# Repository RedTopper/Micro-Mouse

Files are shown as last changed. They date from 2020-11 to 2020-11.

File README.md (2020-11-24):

# Micromouse (sddec20-28)
This repository contains most of the work done by Senior Design group dec20-28
during the Spring/Fall 2020. 

## Team Members
* Joshua Wooi
* Austin Chesmore
* Aaron Walter
* Richard Anderson
* Tyler Fuchs
* Jorge Gomez

## Website
[sddec20-28.sd.ece.iastate.edu](Senior Design Website)

## Resources
This repository contains additional resources generated during the project.
They are stored inside the `resource` directory in the repository root. The
contents of the folders are as follows:

### resource/alg
A\* and Floodfill Algorithms

This is a standalone implementation of the pathfinding algorithm. You can compile
it with `make`. See the README.md inside this directory for more information

### resource/docs
Documentation Files

This folder contains general information about the project, such as a setup guide,
final report, poster, and anything else documentation wise.

### resource/gui
Past User Interface Files

This directory contains a prototype GUI written in Python. We no longer use it in
favor of a web-based UI, but we will keep it here for archival purposes.

### resource/pcb
Current, Past, and Future PCB Designs

These are the Eagle files used to manufacture the PCB of the robot.

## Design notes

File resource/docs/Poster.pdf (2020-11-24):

Richard Anderson, Austin Chesmore, Tyler Fuchs , Jorge Gomez, Aaron Walter, Joshua Woo

# MicroMouse

### Problem Statement:

The goal is to demonstrate how the
interconnection of hardware and software can function together to accomplish a task. In doing so raising interest in related majors.

Client: Dr. Phillip Jones
Advisor(s): Dr. Phillip Jones | sddec20-28

### Technical details:

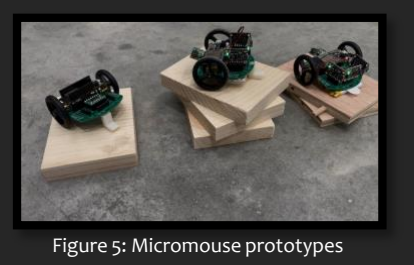
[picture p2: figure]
Figure 5: Micromouse prototypes

GUI: HTML/JS via JSON/WebSockets Framework: C++ (Async)
Floodfill: C++
A*: C++
PCB: Eagle

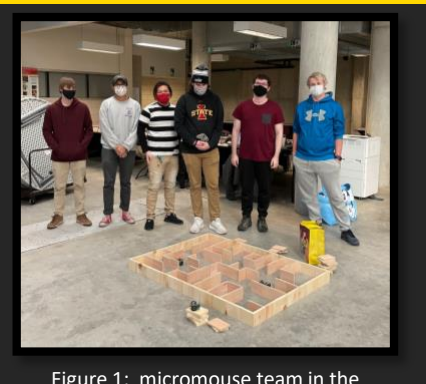
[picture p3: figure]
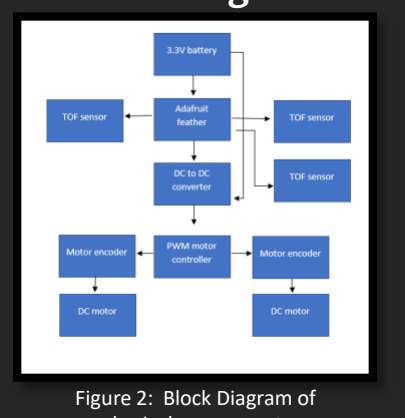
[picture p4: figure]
Figure 2:; Block Diagram of

### Functional Requirements

- Be able to navigate a maze as fast as possible both autonomously and manually.
- Show the location of the mouse in the maze
- Be able to scan for nearby walls forwards and on its sides.
- Move forward, backwards, and turn

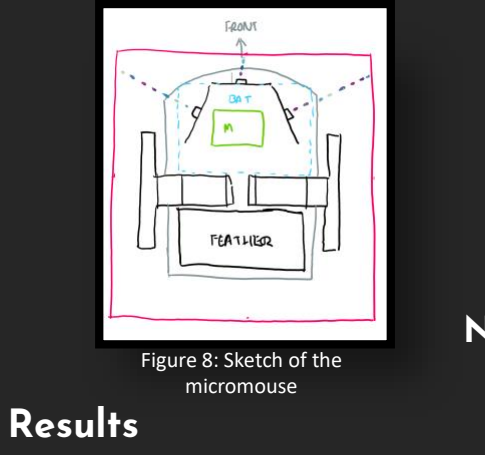
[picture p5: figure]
Results; Figure 8: Sketch of the micromouse

### Non-Functional Requirements

- The path taken towards the maze goal should be optimized in order to be solved as fast as possible
- The mouse will use A* floodfill algorithms to solve the maze.

### Intended user

The intended user of the
micromouse are potential students visiting Iowa State.

### Block Diagram

### Design approach

Our design approach was to select components and hardware that would allow us to build software that would work native. To solve this we selected an Adafruit feather that would work on C++ firmware. And a User interface that would connect to the web server built on the micro controller.

### Testing

Hardware
- Tested the individual hardware components , before testing the components together

Software
- googletest Unit Testing
- Console output for C++ and log files for JavaScript

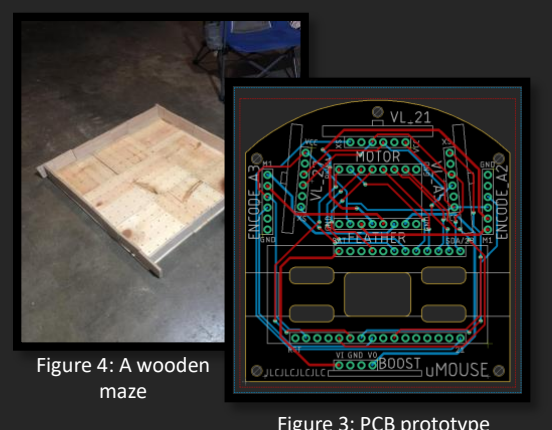
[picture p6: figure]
Figure 4: A wooden maze

Figure 3: PCB prototype

Richard Anderson, Jorge Gomez, Joshua Wooi, Tyler Fuchs, Aaron Walter, Austin Chesmore

For the micromouse project the team dealt with the challenges of working remote during the covid-19 pandemic to deliver a full hardware functional micromouse. The prototype is fully gamepad controllable and can utilize Time of Flight sensors to see obstacles.

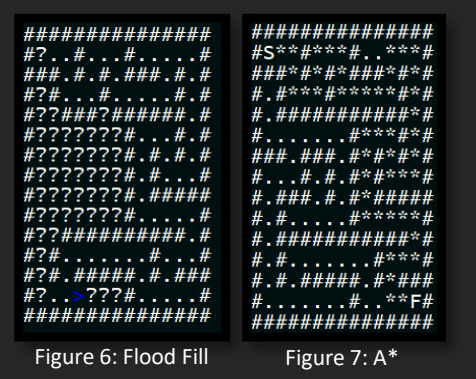
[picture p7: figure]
Figure 6: Flood Fill; Figure 7: A*

Additionally, the team has created functional software for A* and flood fill algorithms that can be implemented on the micromouse in the future

physical components

Figure 1: micromouse team in the order of the names written above

### Flood Fill & A* Traversals

The mouse runs through the Maze using modified flood fill (left), and then uses A* to find the shortest path using the filled map.

### Conceptual Sketch

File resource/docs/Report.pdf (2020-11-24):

# MicroMouse Maze Runner

FINAL REPORT

### Team number: sddec20-28 Client: Dr. Phillip Jones Advisor(s): Dr. Phillip Jones

### Team Members Joshua Wooi Austin Chesmore Aaron Walter Richard Anderson Tyler Fuchs Jorge Gomez

### Team Email sddec20-28@iastate.edu

### Team Website sddec20-28.sd.ece.iastate.edu

### Revised: 2020-11-15

# Table of Contents

1. Introduction | 4
1.1 Acknowledgement | 4
1.2 Problem & Project Statement | 4
1.3 Operational Environment | 4
1.4 Requirements | 5
1.4.1 Engineering Constraints | 5
1.4.2 Functional Requirements | 5
1.4.3 Non-Functional Requirements | 5
1.5 Intended Users & Uses | 5
1.6 Expected End Product & Deliverables | 5
1.7 Relation to Products | 6
2. Specifications & Analysis | 7
2.1 Proposed Approach | 7
2.2 Design Analysis | 7
2.3 Conceptual Sketch | 8
3. Implementation Details | 8
3.1 Previous Work & Literature | 8
3.2 Technology Considerations | 8
3.3 Possible Risks & Risk Management | 9
3.4 Expected Results & Validation | 9
4. Timeline, Resources, & Challenges | 10
4.1 Project Timeline | 10
4.2 Feasibility Assessment | 11
4.3 Team Member Contributions | 12
4.4 Other Resource Requirements | 12
4.5 Financial Requirements | 13
5 Testing and implementation | 14
5.1 Hardware and software description/build | 14
5.2 Hardware Details | 15
5.3 Software Details | 18
5.3.1 Device Firmware | 18
5.3.2 Flood Fill | 19
5.3.3 A* | 19

### SDDEC20-28 1

5.4 Maze Design | 20
5.5 PCB Design | 21
5.5.1 Circuit Schematic | 21
5.5.2 PCB | 22
5.6 Testing Process | 22
5.7 Results | 22
6. References | 26
Appendix I | 27
Operation Manual | 27
Appendix II | 29
Alternative/Initial Version | 29
User Interface | 29
Maze | 31
Appendix III | 32
Tyler | 32
Jorge | 33
Austin | 33
Richard | 33
Aaron | 33
Joshua | 34
Appendix IV | 34

# Figures & Tables

1. Figures
Figure 2.1 High-Level Schematic Design of MicroMouse Prototype | 8
Figure 4.1 Gantt Chart showing timeline | 11
Figure 4.2 Final Bill of Materials and related costs | 13
Figure 5.1 First Prototype Build | 14
Figure 5.2 Breadboard Prototype Build | 14
Figure 5.3 Final Prototype Design | 15
Figure 5.4 Micromouse Ski | 15
Figure 5.5 Micromouse Components | 16
Figure 5.6 Physical Maze Assembled for Prototype Testing | 20
Figure 5.7 Circuit Schematic for Prototype | 21
Figure 5.8 PCB Version 2 | 22
Figure A.1 CLion | 28
Figure A.2 Micromouse Connection | 29
Figure A.3 Micromouse Prototype | 29
Figure A.4 UI version 1. Simple layout | 31
Figure A.5 UI version 2 of the prototype. Web address added | 31
Figure A.6 Version 3 of the UI | 32
Figure A.7 Maze Panels | 33
Figure A.8 Code Part 1 | 36
Figure A.9 Code Part 2 | 36
Figure A.10 Virtual Maze Design | 36
Figure A.11 Virtual Maze Layout | 37
Figure A.12 Virtual Micromouse in Blender | 37
Figure A.13 Importing prototype into Unity | 37
Figure A.14 Standard Floodfill algorithm | 38
Figure A.15 Modified Floodfill | 38
Figure A.16 Goal Searching | 39
2. Tables
Table 4.1 Deliverables Schedule | 10
Table 4.2 Personal Effort Requirement | 12

. Introduction
1.1 ACKNOWLEDGEMENT

This section acknowledges Dr. Philip Jones for his contributions in providing technical advice to the team and Lee Harker for his guidance in sourcing hardware parts and using the EAGLE software. In addition, we would like to thank Jeremy Thurlby and his workshop who helped create feedback for the physical maze design and cutting the maze tiles.

1.2 PROBLEM & PROJECT STATEMENT

Problem Statement:
Our client has outlined a robot that will be able to navigate a maze and autonomously decide and calculate the fastest path to the goal of the maze. This mouse must be able to navigate the maze and run the maze with the fastest path available. This mouse will need to demonstrate how the interconnection of hardware and software can function together to accomplish a task.

Solution Approach:
A MicroMouse Maze Runner Showcase.

People project that there will be many more computer/electrical/software-based jobs than there are people to fill the jobs, so we need to try to give a reason for future ISU students to consider robotics-based curriculums. This project serves to showcase the capabilities of engineering students from multiple disciplines at Iowa State University.

The expected outcome of this project is a functioning micromouse unit(s), capable of both autonomous and/or remote-control functions, that can traverse through several different maze designs effectively. Our expected outcome was near our completed design, but there were some major missed goals of our project. The main goal that we were not able to accomplish was the traversal of the maze autonomously. While our micromouse can navigate the maze with controller input, we were not able to finish the autonomous version of the maze navigation. We also did not finish a graphical user interface. The client outlined a GUI to draw the maze and update in real time, but we never finished this feature.

1.3 OPERATIONAL ENVIRONMENT

The product of this project was to be able to operate a micromouse in a controlled environment. We designed the maze to have a smooth surface with adjustable walls. This will ensure the maze is stable for the micromouse to navigate. The operation of a micromouse outside of this environment condition is unexpected and undesired. We expect the environment to be modular and transportation friendly so people can use it anywhere with enough space.
1.4 REQUIREMENTS

### 1.4.1 Engineering Constraints

| ● The memory size on the Feather was a strict 520 kb

- The ROM size of the Feather is 4MB
- The micromouse requires a flat smooth surface for the maze
- Hardware is inherently unreliable

### 1.4.2 Functional Requirements

Functional requirements of this project would be that the mouse is able to move through the maze, is able to map a maze to a maze model, is able to find the shortest path of the maze model and is able to follow paths through the maze. We also must have a maze that can fit the micro mouse, be modular, transportable, and solvable by the mouse.

### 1.4.3 Non-Functional Requirements

Non-Functional requirements of the project are that the mouse should be accurate, reliable, and sturdy. Our maze will have to be of quality materials so that it is able to last long when we reconfigure or transport it.

1.5 INTENDED USERS & USES

As a showcase project, the intended user of a micromouse is anyone with latent interests in Robotics. Our team designed this project to inspire and encourage anyone to pursue a degree in the STEM field.

1.6 EXPECTED END PRODUCT & DELIVERABLES

During this project there were many timelines that COVI-19 forced us to change due to circumstances we had no control over. Therefore, some deliverables were either delayed indefinitely or removed entirely from the scope.

Components ordering (2/21):
We submitted our Bill of Materials for ETG to approve, so we can continue to make progress on Prototype 1.

Delay (3/20)
When classes transitioned into a virtual environment, we had to delay the deliverables with Prototype 1 and all future hardware related operations until further notice, since the university had implemented safety precautions against COVID by closing access to the lab equipment on campus to students.

GUI (3/27)
The team created and delivered the first prototype of the GUI to the client.

Virtual Maze (3/27)

The team developed a virtual maze and robot with the unity engine so work could continue the prototype’s embedded algorithm while conforming with virtual instruction guidelines.

GUI 2 Electric Boogaloo (4/10)
The team designed the GUI to be more user-friendly and included a mapped maze.

Hardware Constructed (4/18)
The team constructed the parts to ensure everything was functioning as expected.

Second Round of Parts (9/15)
The team ordered a second round of parts as a contingency for technical failures during tests.

Software Testing (9/29)
The team began software testing on the Feather so that we can continue to develop hardware and software integration.

Maze cut & Assembled (10/10)
The team cut the physical maze and assembled it to test the micromouse once we completed the prototypes.

PCB Design (10/27)
The team ordered, received, and assembled our first prototype on a working PCB.

Prototype Assembly (11/6)
The team delivered a working prototype that someone can control with an Xbox One controller to the client.

1.7 RELATION TO PRODUCTS

We expect that a competition-ready micromouse will have various iterations before it is up to professional standards. The team believes that there is still room for improvements on our first prototype, and it is therefore unfit for a micromouse contest. That said, we believe that this prototype has met all the requirements and expectations of our client’s project. A micromouse should not be more than 25cm by 25cm, in length and width, with no restrictions on the height of the micromouse. Also, it must use a source of energy that does not involve a combustion process. Next, the micromouse should not leave behind parts of itself in the maze while solving it. Lastly, micromice should not jump, fly, or climb over any walls, and it should not burn, cut, or damage the walls of the maze or maze itself. This mouse is 10.2cm x 10.2cm which is smaller than most other micromouse units. Furthermore, a lithium-ion 3.7V battery powers the mouse.

## 2. SPECIFICATIONS & ANALYSIS

2.1 PROPOSED APPROACH

The team decided to prototype the project using an Adafruit Feather as a controller, to allow for a more robust implementation using the Feather’s features. The team also chose the Feather since it can support all the peripherals for the project, such as I2C signal bus, and analog to digital signal conversions. The feather also has built in support for Bluetooth and Wi-Fi functionalities that satisfies the requirements of our client for an optional wireless communication system with a user.

We had two prototyping phases for hardware in this project. The first phase was assembling components on a breadboard, and the second phase was designing and having a PCB fabricated. The plan when starting the project was to use Python to interface the software and hardware, due to the flexibility of the language in its compatibility with other types of software. For instance, we would write the maze algorithm, the GUI, and hardware interface in Python with different libraries. Additionally, we utilize C++ along with several Arduino libraries to program the functionalities of the micromouse.

We ordered an additional set of components, so that we would have spares if potential errors or hardware malfunctions occur.

2.2 DESIGN ANALYSIS

During the first semester, the project team thoroughly researched the specifications that the Micromouse project will need to meet. Through this research, the team developed a components list. We brought the component list for approval by Dr. Jones and ETG, to ensure that the selected components were reasonable for the purposes of the project. In the second semester, the team focused on testing the components and integrating them into a full micromouse prototype. At the end of the second phase of the design process the team transitioned into testing integration of software and hardware to ensure functionality. At this point, the team decided to split into two branches for software and hardware. Towards the end of the project, the team converged both branches back together to reintegrate the software and hardware side of the project.

2.3 CONCEPTUAL SKETCH

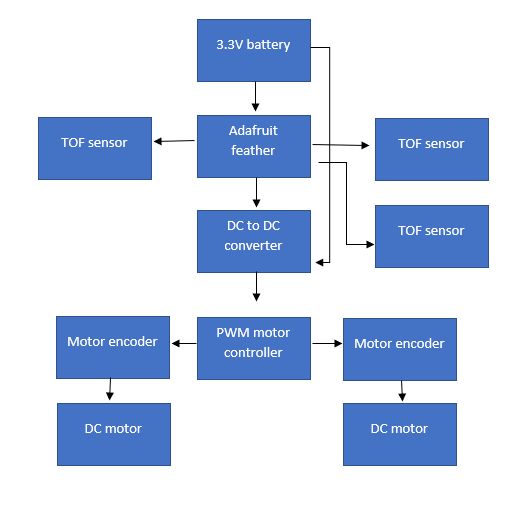
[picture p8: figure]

Figure 2.1 High-Level Schematic Design of MicroMouse Prototype

This is a conceptual design of how the micromouse will be created and interact with all the components that were selected by the tram for the project. It shows how the micromouse functionality will live on the Adafruit feather, while the feather will then command the other components to enable the micromice hardware functionality

## 3. IMPLEMENTATION DETAILS

3.1 PREVIOUS WORK & LITERATURE

Classwork here at Iowa State University has laid a foundation that we can reference, specifically CprE 288 in its autonomous robot project. This project has had a long history, and there are plenty of online articles and documentation that will help us in designing the micromouse. There are also micromouse competitions that should yield even more documentation that our team can reference for our project. For our PCB design we utilized a software program called Eagle and referenced a tutorial by Jim Blom (Blom, Jim).

3.2 TECHNOLOGY CONSIDERATIONS

The technology that we incorporated for our micromouse was cost effective and modular. The team selected widely available components to integrate it into the prototype design. By using off the shelf components, the project will less likely have quality issues, such as solder bridging or improper design. This removes several potential failure points, allowing for the project to be bug tested more effectively. However, one weakness of using these types of components is that there is less controllability of the specification.

Other considerations include the amount of memory available to our team on the feather. We need to be diligent on how large our software is and how much memory it will consume when running the maze.

3.3 POSSIBLE RISKS & RISK MANAGEMENT

Prototyping the mouse was the most worrisome of our project, getting all the different pieces to work together included. After we learned what hardware can work with what software, prototyping became much easier and we were able to create more designs.

When we tested components, it was important to be careful as to not connect pins where they should not be. This became apparent when a team member put a 12V supply on a GPIO pin and subsequently fried our first Feather. Other risks include damage to our components, when moving them they needed to be either secured in a safe storage container, or back in the foam protection they came packaged with. Luckily, we did not have any issues with bent pins from transportation.

Cost was a major part of our potential risk when designing our micromouse robot. The cost to the maze can range from 10s to 100s of dollars. We only ended up spending about $40 on the maze itself but looking back we should have spent more.

The final risk that we considered was that none of our members of our team had any prior experience with PCB design. This was why our team spent many weeks designing the PCB. To mitigate this risk, we had two team members, with instructions from our mentor, build and practice with Eagle software to become more efficient.

3.4 EXPECTED RESULTS & VALIDATION

The desired outcome, as outlined by the client, is a micromouse that can solve and run through a maze on its own. It will also have a display that people will use to run the program and can respond to user input. The user will have the ability to control the mouse with a controller and the mouse will respond accordingly.

## 4. TIMELINE, RESOURCES, & CHALLENGES

4.1 PROJECT TIMELINE

Table 4.1 Deliverables Schedule

Dates | Deliverables
1/20-2/21 | We constructed our groups and scheduled bi-weekly meetings with the clients. The team researched parts for the robot prototype and ordered them. The team began prototyping.
2/22-3/20 | The university transitioned to online formats and this included our team. We developed a virtual platform for our micromouse to navigate a maze and allowed us to test any maze path finding.
3/21-4/10 | Prototypes of the GUI, maze and Virtual maze delivered to the client. The team decided to move work to a virtual platform built in Unity due to COVID-19.
4/11-4/18 | Our team received our parts after COVID-19 delayed them. Hardware testing began with breadboard and components.
4/19-5/2 | Project Design Document drafted and finished; Project website updated.
Break | Summer Break
8/20-8/31 | The team scheduled meetings with the client.
9/1-9/14 | Our team Encoders tested. Round 2 of parts ordered.
9/15-9/28 | GUI connecting via Wi-Fi, microcontroller code continuing. PCB design beginning. Hardware testing continued. Round 2 of parts received.
9/29-10/9 | A* algorithm developed. Updated version of GUI developed. Web server on feather developed and tested.
10/10-10/26 | Maze cut and assembled. Final GUI developed to incorporate a maze drawing panel. First version of PCB design and presented. A* finalized. Modified flood fill development.
10-27 - 11/9 | PCB delivered. Prototype 1,2, and 3 fabricated. Input to micromouse demonstrated to the client. Modified flood fill finalized.
11/10-11/19 | Prototype 1 & 2 fully functional. Project Document drafted and finished. Build Guide created for future teams.

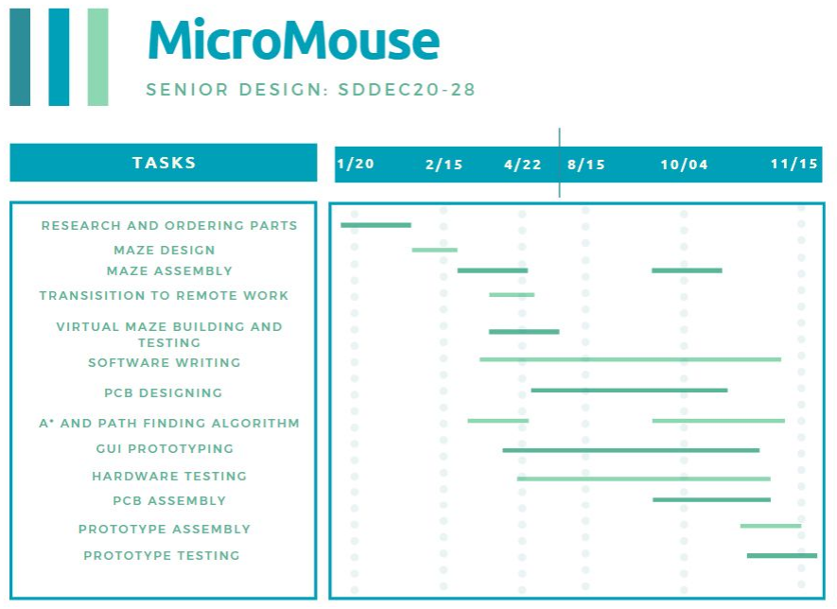
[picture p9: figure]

Figure 4.1 Gantt Chart showing timeline

4.2 FEASIBILITY ASSESSMENT

- Autonomous maze navigation
- Wall detection without getting stuck in a loop
- Detecting the goal of the maze
- User input controls
- Bluetooth protection from other devices
- Maze Design
- Price - keeping the price in check so we do not blow the budget.
- Mobility - being able to transport the maze while also being large enough to be complex

4.3 TEAM MEMBER CONTRIBUTIONS

Table 4.2 Personal Effort Requirements

4.4 OTHER RESOURCE REQUIREMENTS

The main outside concern is where we can store the maze while it is being built. As per the client, they would like a maze that is at least 9 feet by 9 feet, so this will require a large open space.

Team Member | Contribution | Prev semester | This semester | Total
Richard Anderson | My contributions were the algorithms for the micromouse, specifically the modified flood fill and A* algorithms, as well as testing the algorithms correctness and modifiability to for hardware use | 47 | 75 | 122
Austin Chesmore | My contributions to the project we to primarily assist with testing the hardware components. I also assisted with assembling/soldering of the prototypes and the component selection | 53 | 105 | 158
Tyler Fuchs | My main contribution to the group was working on the UI in its many forms and building the physical maze. In total I built 4 different UIs to test and two sets of maze walls. | 42 | 91 | 133
Jorge Gomez | My greatest contribution to the team was the scouting of hardware and PCB research and design. | 41 | 74 | 115
Aaron Walter | My contribution was writing the firmware for the feather. I got a mini web server working on the Feather and all of the “drivers” written to work with the hardware. I also helped a lot with the PCB designs. | 57 | 117 | 174
Joshua Wooi | My contributions were designing and revising the PCBs and some of the soldering work. | 37 | 70 | 107

4.5 FINANCIAL REQUIREMENTS

For the Micromouse project our budget is set at $500 per semester with the ability to extend beyond if we need to. The team split the budget between the hardware and physical components. We decided to construct the maze from rough cut pine to keep the price down. In total the physical maze ran a price tag of $32.15. Whereas someone can use the hardware between different prototypes. During the first half of the project the team spent $316.87 on the hardware components. On the other hand, we used $320.42 for the second set of components. In the end the sum cost of all hardware came to a cost of $605.14. As depicted in Figure 4.2, one of the greatest costs is the ToF sensors. We found a different component for future use. The suggestion is to go from using the VL6180 ToF sensors by Adafruit and moving towards using the VL680X ToF sensor from Pololu causing the price of sensors to go from $13.95 per sensor to $8.49 per sensor. Overall, the team kept costs the allowed amount and new, cheaper components are being thought of for future use.

Figure 4.2 Final Build of Materials and Related Cost

Item# | Item type | Qty | Cost | Subtotal | Part# | Supplier | Supplier#
1 | Feather board | 4 | $20.95 | $83.80 | 3591 | Digi-Key | 1528-2514-ND
2 | Motor Controller | 4 | $3.42 | $13.68 | 713 | Digi-Key | 2183-713-ND
3 | Magnetic Encoder | 8 | $7.95 | $63.60 | 4761 | Digi-Key | 2183-4761-ND
4 | Wheels | 8 | $3.75 | $30.00 | 1452 | Digi-Key | 2183-1452-ND
5 | Motors | 8 | $18.95 | $151.60 | 3053 | Digi-Key | 2183-3053-ND
6 | DC/DC 3.7 to 12v | 4 | $2.99 | $11.96 | | Canton Electronics
7 | ToF Sensors | 12 | $13.95 | $167.40 | 3316 | Digi-Key | 1528-1815-ND
8 | Battery 3.7v (4.2) | 4 | $9.95 | $39.80 | PRT-1381 3 | Digi-Key | 1568-1492-ND
9 | Encoder Wires | 8 | $0.95 | $7.60 | 4762 | Digi-Key | 2183-4762-ND
10 | .3.6-pin 0.1" Short Break-away Male Header - Pack of 10 | 2 | 4.95 | $9.90 | 3009 | adafruit
11 | 36-pin 0.1" Short Female Header -Pack of 5 | 2 | 7.95 | $15.90 | 3008 | adafruit
12 | 0.1" 36-pin Strip Right-Angle Female/Socket Header (5 pack) | 2 | 4.95 | $9.90 | 1542 | adafruit
| TOTAL | 62 | | $605.14

## 5 TESTING AND IMPLEMENTATION

5.1 HARDWARE AND SOFTWARE DESCRIPTION/BUILD

Testing of the hardware components and assembling several testing prototypes was necessary to ensure that the teams ordered components would function correctly. At an early point in the project the team moved towards creating a virtual maze environment that team members could test the micromouse in. During this time, another team member was constructing the physical maze. However, the team ended up testing the first hardware prototype with limited functionality due to component shipping wait times, and thus the team scrapped the virtual maze for testing and transitioned into the physical maze.

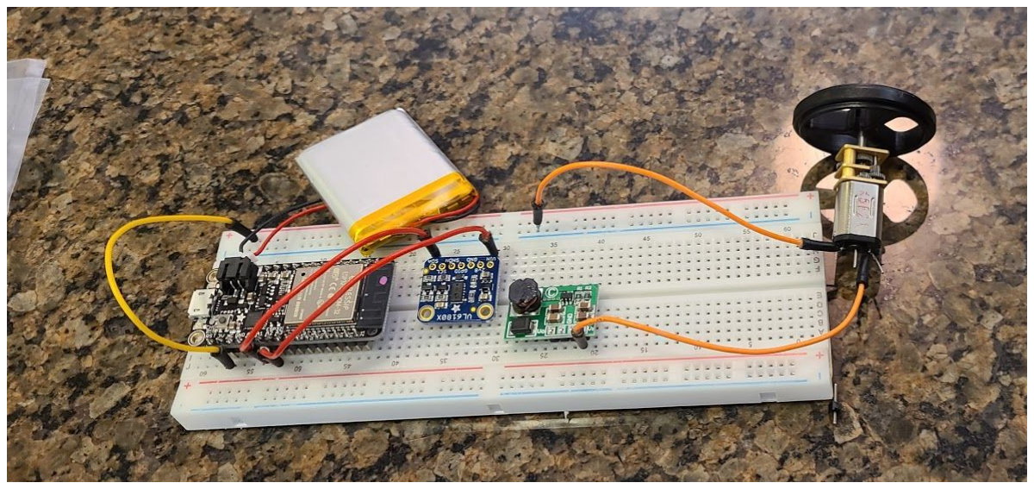
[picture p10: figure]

Figure 5.1 First Prototype Build

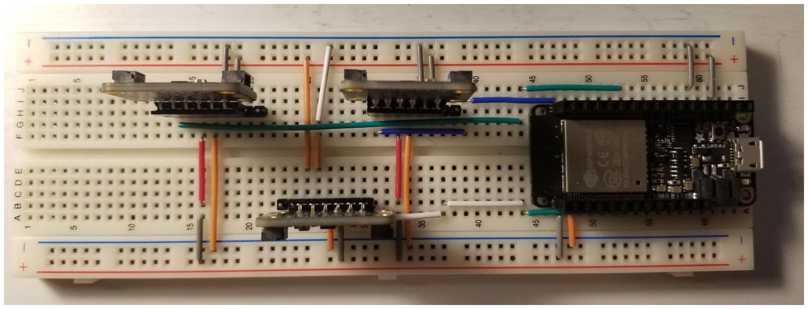
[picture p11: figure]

Figure 5.2 Breadboard Prototype Build

This hardware prototype at the end of semester one used a breadboard and the available components, for basic proof of concept design tests. We only incorporated a single wheel and sensor into the design to demonstrate that all components work together as intended. Additionally, after the first round of testing, the team would then move to a more permanent hardware design using PCB instead of the breadboard.

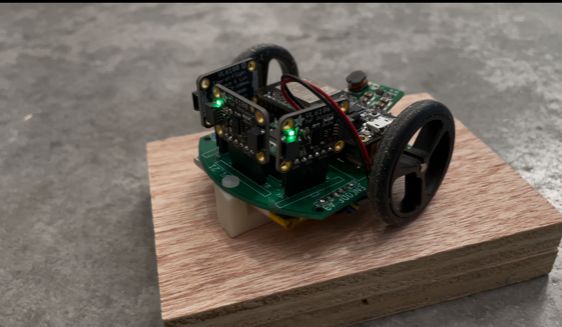
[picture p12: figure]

Figure 5.3 Final Prototype Design

The current micro mouse design is currently being prototyped using a final PCB design for proof-of-concept design tests. The team integrated all components onto the PCB along with a 3D printed ski. For this prototype we were able to utilize the C++ software that was written by the team to achieve movement functionality.

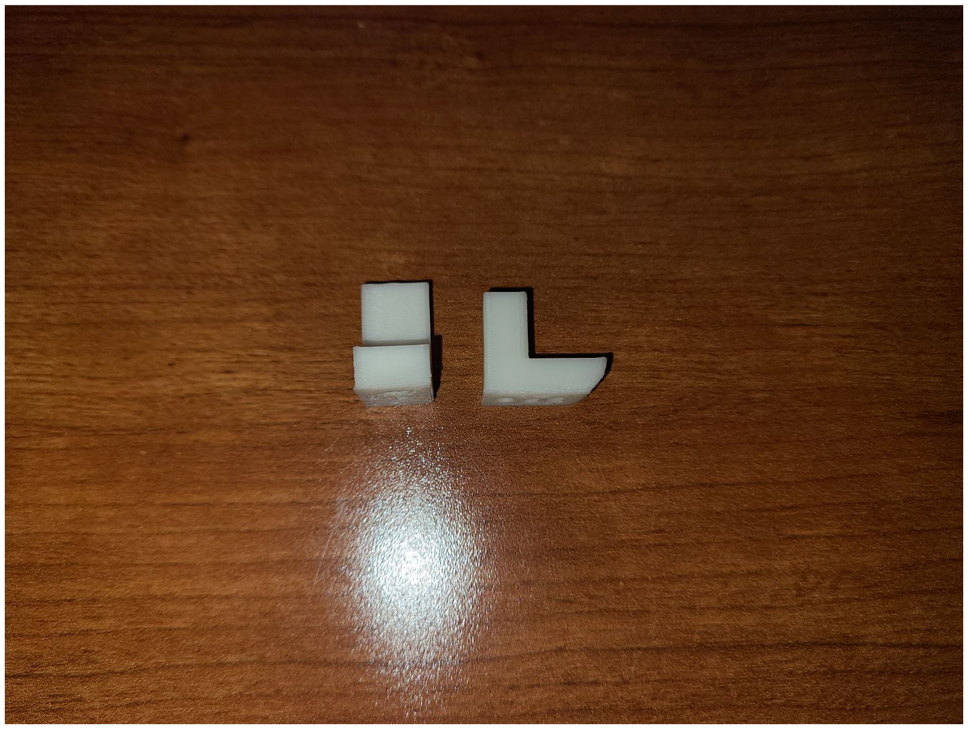
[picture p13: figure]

Figure 5.4 Micromouse Ski

Additionally, the project team 3D printed a ski that is seen implemented in figure 5.2. This ski allowed the prototype design to function with only 2 wheels, while also allowing for improved stability.

5.2 HARDWARE DETAILS

The team selected the components members could easily integrate them into the micromouse. By using prebuilt components, we reduced the risk of having issues with the quality of the components. This would allow for the team to focus on the main objectives, rather than having to troubleshoot smaller issues such as faulty components.

Below, you will find a breakdown of the components used in the construction of the micromouse along with the quantity of parts used per micromouse, and the reasoning behind why the team chose them.

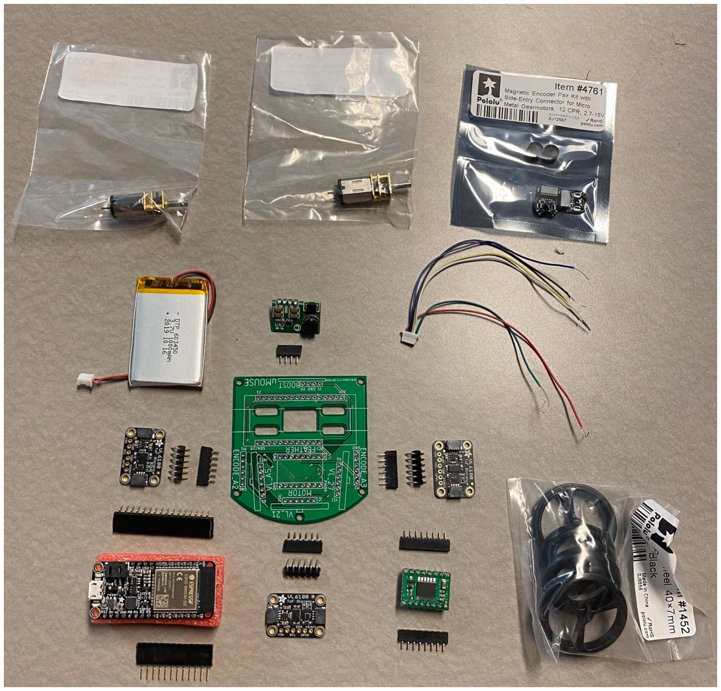
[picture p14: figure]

Figure 5.5 Micromouse Components

- HUZZAH32 ESP32 FEATHER MALE HDR
| x1
- The Adafruit Feather is a compact but powerful development board with in-built functionalities that meet all our requirements. It has Wi-Fi capabilities, programmable in C/C++, uses I

2C for the sensors, PWM for the motors, ADC/DAC pins for controls, and GPIO pins for everything else.

- TB6612FNG Dual Motor Driver | x1
- This Motor Driver can control up to two motors simultaneously and allows us to tune the rpm of the motors as needed, using feedback from the encoders.
- Magnetic Encoder Pair Kit With Side-Entry Connector for Micro Metal Gearmotors, 12
CPR, 2.7-18V | x1
- The encoders allow for precise rpm configuration and are compatible with the motor in the components list.
- WHEEL 40X7MM PAIR - BLACK | x2

- These wheels are compatible with the motors on this list. In addition, they are rubber lined and will do well on different surfaces. Lastly, the axles are made of plastic to eliminate any possible problems with the encoders.
- GEARMOTOR 220 RPM 12V METAL EXTD | x2
- These motors meet our size requirements, are powerful and fast for their size, include gearboxes, are compatible with a wide range of wheels and the encoders.
- 12W DC-DC Converter Boost 2V-12V | x1
- This boost converter increases and regulates the voltage output of the battery to supply power to the motors.
- VL6180 TIME OF FLIGHT DISTANCE
| x3
- These distance sensors use I²C for fast communication with the Feather and fit well within the size for the micromouse.
- B6-PIN FEMALE JST SH-STYLE CABLEATTERY LITHIUM 3.7V 1AH | x1
- This battery meets our needs to power the Feather, at 1000 mAh, is rechargeable, and is relatively compact.
- 6-PIN Female JST SH-STYLE Cable
- These six pin male connectors fit well with the encoders.
- 36-pin 0.1" Short Break-away Male Header (10pack) ... | x1
- These male header pins are to be soldered onto components so it can be attached to header sockets on the PCB.
- 36-pin 0.1" Short Female Header (5 pack) | x1
- These female header pins are to be soldered onto the PCB so it can accept components.
- 0.1" 36-pin Strip Right-Angle Female/Socket Header (5 pack) | x1
- These right angle male pins are to be used to allow the VL6180 Time of Flight Distance sensors to stand perpendicular to the PCB.
- PCB | x1
- The PCB was the only piece of hardware that was designed by the team for the explicit purpose of housing/organizing the above components. In doing so, it gives the micromouse a more cohesive look. We decided on using header pins/sockets style connections for a secure but impermanent connection between the PCB and the components. This was done so components can be easily replaced. This PCB was designed using Eagle, a scriptable electronic design automation application, and went
| through a few iterations before arriving at the final version that was used. More
| information on the PCB can be found in Appendix II.

5.3 SOFTWARE DETAILS

The Micro-Mouse project has multiple software components. There are three main parts, the GUI, the software to bridge the hardware devices, and the maze algorithms. Each component was essential in delivering a maze running micro-mouse that met all of our client’s requirements.

The device firmware that interfaces with the hardware components was written in C++. Many different functions were needed that were not originally foreseen when beginning the prototyping phase. For instance, a function was required to slow down the acceleration of the motor controller due to a bug that would shut down the feather if the speed was set from a stop to full speed.

The User Interface has gone through many different changes and versions. To begin the project, we had selected a GUI library in python called PyQT5 to write the graphics. The plan was to write a simple panel with a spot for a console, image holder for mapping the maze, and a few buttons for functionality. After a few versions and upgrades to this plan we ran into an issue with drawing the maze and updating it during the navigation of the maze. Instead, our group moved to developing a web-based GUI that will utilize JavaScript to run commands and access the basic web server running on the Adafruit Feather. HTML5 would provide the imaging mapper tag that would help to draw the maze and fill in the missing functionality that the PyQt library was missing.

The maze solve algorithm is used so that the mouse can navigate and then solve the maze. The algorithm first does a modified flood fill to build a maze model, and then uses an A* algorithm to find the shortest path. The algorithm is gone into further detail in section 5.3.2 and 5.3.3.

5.3.1 DEVICE FIRMWARE

The device firmware has many different components that make the device function. It implements a lightweight MVC framework written in C++.

Access Point
The first component is the AP Station software that allows the ESP32 to host a wireless hotspot for the “command center” client to connect to. The micromouse firmware can also be used to connect to a client, to then connect to an existing hotspot if needed.

Async Web Server (Controllers and Views)

The firmware also includes an asynchronous web server to allow the command center to communicate with the micromouse in real time. There are two parts to this web server: the JSON REST API and a WebSocket. The REST API allows the client to query the status of the robot: distance traveled, sensor distances, speed, and other real time information. The WebSocket allows the command center to send movement commands to the robot. The valid inputs are currently keyboard and any X-input controller.

Components (Models)
The firmware includes a lightweight “driver” for each of the devices connected to the mouse. There are components set up for the encoders, motors, and time of flight sensors. These components control the logic of the hardware and provide information to the pathfinding algorithm.

## 5.3.2 FLOOD FILL

The mouse uses a modified flood fill algorithm to scan the physical maze. How a typical flood fill algorithm works is it scans all possible directions from the current cell, and then recurses down each of the cells that are able to be visited, until every cell has been visited. This is the behavior of the typical flood fill, whose pseudocode can be found in Appendix IV.

In terms of the micromouse however, this algorithm is not satisfactory, since the mouse needs to physically move throughout the maze. With the described algorithm, the mouse would be expected to teleport back to previous cells, as well as already knowing the maze. We needed to modify this algorithm so that the wall-checking instead uses scanner distances to check for immediate walls, as well as consider mouse movement and directions, and moving the mouse to previous cells during recursion. In our implementation, we create a 2d array of binary numbers, and use the 5 rightmost bits to keep track of the north, east, south, and west walls, as well as if the related cell has been visited.

The updated flood fill starts with the mouse using its sensors to scan the immediate left, right, and forward cells from its current direction, and then adding those scan results to the maze map. From those scans, if any of them are 0 (meaning no wall), then the mouse will turn towards the “wall-less” direction (if need be), move forward 1 cell, and then recurse down in the algorithm with that cell. Once the cell has gone down each direction, the mouse turns towards the direction opposite of what the mouse was at the start of the current recursion level, then moves forward, effectively moving the mouse backwards to where it was before recursion. The cell is also marked as being visited so the mouse will not go back down the direction. The modified version of the flood fill can be found in Appendix IV

5.3.3 A*

Once the mouse has been flood filled, it can use an A* algorithm to find the shortest path from the starting position to the goal.

To find the goal of the maze, we obtain the map through the flood fill process. Then, we have another function which searches the maze map for a 2x2 closed loop, meaning we make sure that a northwest cell can go to the south and east cells, and the southeast cell can go to the north and west cells. This functionality can be seen in Appendix IV.

Once we know the end goal, we have the heuristic to be used for our A*. From there, it's a matter of getting a selected path, taken during the A* process. With this path, we will be able to get instructions that the micromouse can follow to solve the maze.

5.4 MAZE DESIGN

The client outlined that the micromouse maze needed to be mobile and reconfigurable. To combat these challenges our team designed a maze that used wood tiles/panels in combination with a peg board pattern where the walls could be moved around to create new maze patterns. This is shown in appendix II. Figure 5.6 is an image of the maze we built when testing our prototype micromouse. We did not use the maze panels for this test because we wanted a complex design for the robot to navigate through.

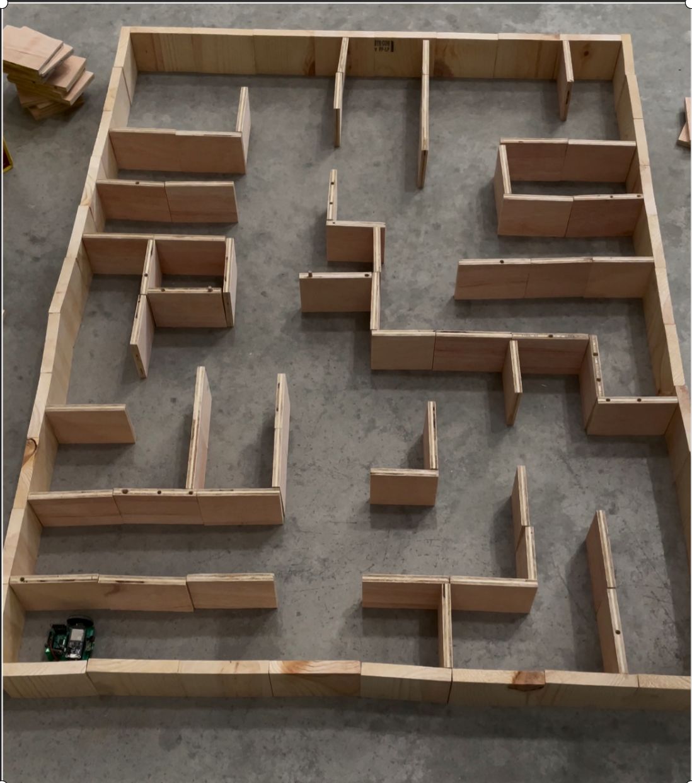
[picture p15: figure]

Figure 5.6 Physical Maze Assembled for Prototype Testing

These maze walls are the standard 3 inches high. This was found to be the standard for half size micro-mice. For the maze panels, they were cut from a 12” x 8’ board of rough-cut pine. Since it was a rough cut board we were forced to cut a little further down and the panels came out to be 11.25” x 11.25”. This required the panels to precisely cut and therefore we spoke to Jeremy Thurslby, and with his help we cut the panels using a CNC router which yields perfectly symmetrical panels that can be connected together.

## 5.5 PCB DESIGN

## 5.5.1 Circuit Schematic

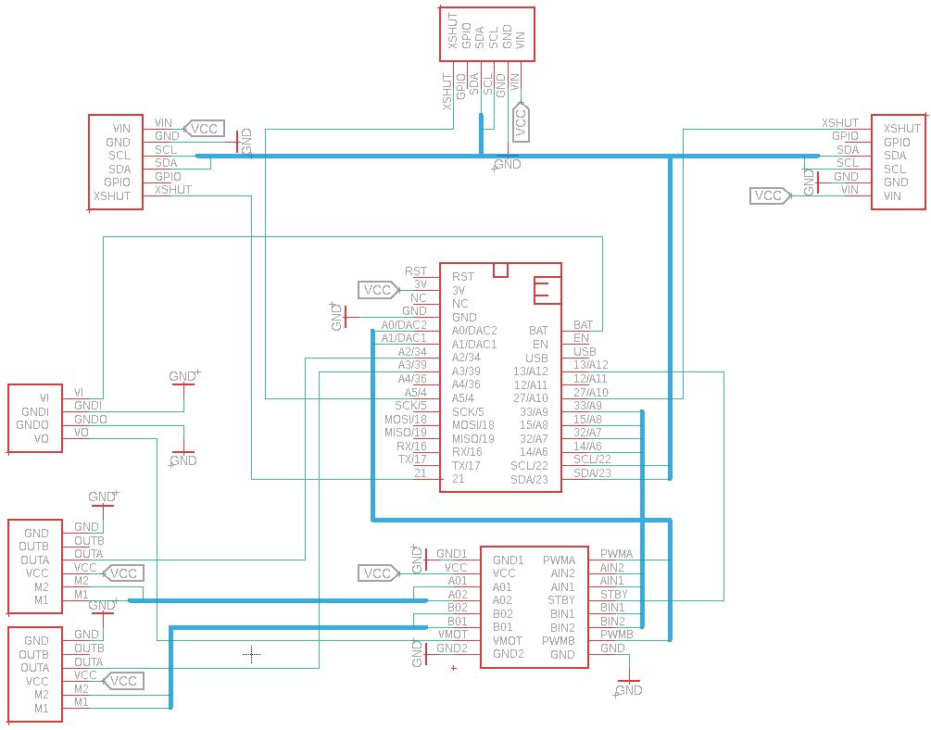
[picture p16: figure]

Figure 5.7 Circuit Schematic for prototype.

The circuit schematic file (depicted above) illustrated through Eagle, which describes a low-level interpretation of our initial design, and details the interconnections between our components in the PCB. The feather board serves as our main controller for most of the operations through the BAT, 3V, and most of the GPIO pins. The 3 distance sensors sit at the front/top and communicate with our Feather board via I2C in the SCL and SDA pins. Additionally, we allocated 3 GPIO pins as ‘XSHUT’, which will effectively shut down a targeted sensor, should we decide it is necessary. The 3V, which outputs a steady 3.3V through an in-built regulator, serves as the pull-up supply for most of the components. However, this pin is limited to a 500mAH output, which will not be sufficient to power the motors. The BAT pin, which outputs a 3.7V supply, is therefore boosted to a steady 12V to power the motors, through the motor controller. Most of the other GPIO pins are dedicated to the ADC and PWM pins which decide the rpm at which the motors operate. Feedback from the motor, provided by the encoders, is then connected to the Feather. All these components are externally powered by a 3.7V, 1000mAH rechargeable battery, which is rechargeable through the microUSB port on the Feather.

## 5.5.2 PCB

Rather than using any surface mounted pads, we created custom footprints to solely use through-hole vias to accommodate header pins. Using Eagle’s auto-routing function, we produced a layout (depicted below) that we used for our MicroMouse prototype. The produced layout had multiple vias that connected traces between the 2 copper layers, and while we had reservations about this design from an aesthetic standpoint, we do not expect that it will hinder performance in the slightest.

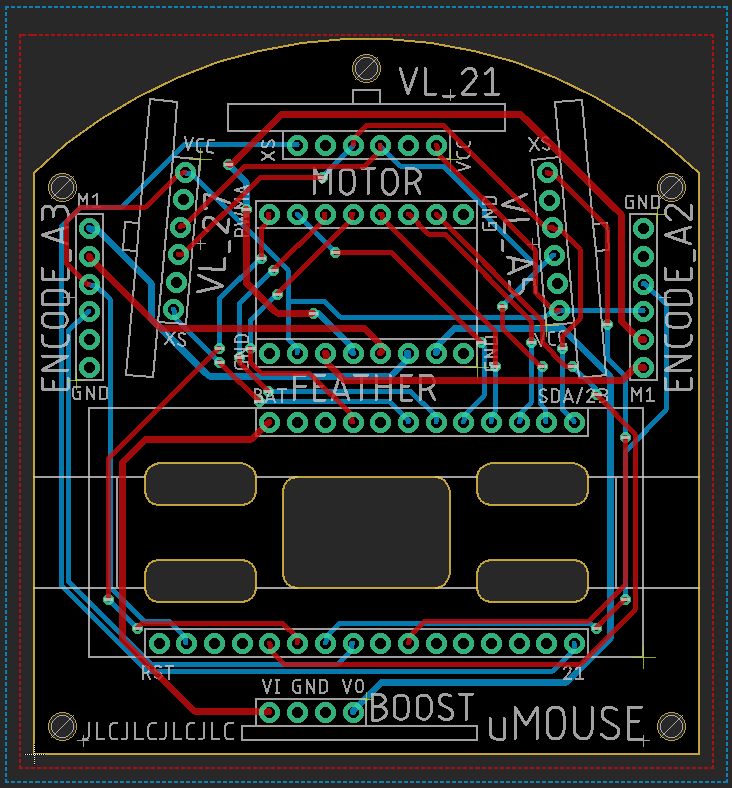
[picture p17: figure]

Figure 5.8 PCB Version 2

5.6 TESTING PROCESS

Once the software was built and flashed onto the micromouse we were able to test the basic web server that was hosted on the Adafruit Feather. An interface between the software and hardware was tested by flashing this firmware onto the mouse and seeing any changes in the robot’s responses. This development was all done in CLion as described in Appendix I. We also tested some of the hardware controllers with Google Test, which is a c++ unit testing library.

5.7 RESULTS

Throughout the duration of this project our team has put in countless hours from design planning to PCB drafting, to sawing the maze, to draft writing. Our client outlined a few main goals for us to work towards along with a project statement. The main goals we had were to:
1. Build a working micromouse that can manually navigate a maze.
2. Build a User interface so any person can test the functionality of the micromouse
3. Allow the robot to navigate the maze autonomously and choose the fastest route.

Along with these outlined criteria the team established success criteria for the team to judge the outcome of the project. While our team’s timeline and results were affected by the COVID-19 pandemic, the team persevered and met the majority of the self-imposed goals. Below is a list of the success criteria that the team created, along with the results and explanations for meeting or not meeting criteria.

### 1. Create a working micromouse design that has easily replaceable components

The results of the success criteria were that we successfully created a couple of fully operational micromouse prototypes that had easily replaceable components. this was accomplished by utilizing male and female header pins to solder to the PCB and components, as opposed to soldering all components directly to the PCB

### 2. Produce a micromouse prototype that utilizes a PCB

The result of the success criteria was positive as we received our components and started prototyping originally with breadboards. However, breadboard testing created several reliability issues with faulty connections. these “bad connections'' prevented the components from communication effectively over I2C. This pushed the team to get a PCB design created and ordered. after the PCB prototypes were integrated into the prototype design the micromouse functioned much more reliably before.

### 3. Allow for micromouse to have a manual user operational mode

The result of this success criteria was successful. The web server that is hosted on the Feather allows the user to send commands from controller input, and the mouse will respond accordingly at a rate of 50 commands per second. The number of commands was necessary for the controller input to accurately reflect the changes in the input. In addition to the web server, an acceleration class was created to deal with a bug with the motor controllers. If the encoders were set to 1,1 (left, right) from 0,0 the program would crash, and the Feather would need to be reset. An acceleration class handled the input from the user interface and slowly scaled the speed the motor controllers received. For example, if a command of 1,1 was sent to the Feather over the web server, the firmware would set the motor controllers to 0.2, 0.2 and after 200 milliseconds would increase by increments of 0.2 until the speed matched the input.

### 4. Use a flood fill based algorithm to run through the entire maze while mapping all

the walls and the end goal.

The results of this success criteria are a mix of success and failure. We have a working modified flood fill algorithm that can search through a virtual maze, and create a map based on it using theoretical sensor input, mouse movement, and mouse turning.

Unfortunately, we were not able to get the flood fill working with the physical mouse and physical maze in time, but we believe the algorithm could be modified or reused with functions that physically move the mouse wheel or use the mouse’s sensor output.

### 5. Use an A* algorithm to find the shortest path between the starting position and the

end goal.

The result of this success criteria is also a mix of success and failure. We do have a working A* algorithm that takes the generated maze map from flood fill and generates the shortest path from the start to the goal. The output of our A* is the instructions the mouse will need to execute to reach the end goal of the maze.

Unfortunately, the mouse does not currently use this list of instructions, but the functionality is there for when a later group is able to make the mouse execute the instructions one by one.

### 6. Create a GUI interface that will allow for a user to easily interact with the

micromouse platform

The outcome of this success criteria is also a mix of success and failure. The team made a move late in the development process to switch the python user interface to a web-based. The transition was made to allow more team members to contribute to the development of the user interface. Some of the functionality that was required by the client was completed. The web-based UI displays information to the user that the client outlined, along with input being received from a controller input. The functionality that was missing was mapping the maze to the interface. This functionality was also missing from the Feather, so implementation was not completed on either front.

7. Micromouse prototype should comply with full size compilation standards.

When it comes to micromice, there are two options the team explored, full size or half sized. Due to the size of the parts the team selected, we decided on going with the full size bot. The team attempted to create a mouse as small and compact as the full size would allow, leading to nearly being considered half sized mouse. The standards for a full size include:

- Self-Sustaining - Should not be controlled or use an energy source that involves a combustion process.
- Structurally Sound - Should not leave any parts behind while traversing the maze.
- Movement Restrictions - Should not jump, fly, or climb over, as well as damage, the maze walls or floor.

- Size - Should not be more than 25 centimeters in width or length, but there is no restriction to the height, as stated by the IEEE SAC 2018 micromouse competition rules.

The current design of the micromouse has met these expectations except the rule regarding not controlling the micromouse, however this was due to our client requesting the user be able to manually control the mouse. No current issues with its structural integrity. Lastly, the micromouse measures 10.2cm x 10.2cm.

8. Create a portable maze that will be solved by the micromouse.

The result of this success criteria is also a mix of success and failure. We currently have a bunch of timber that we are able to form in the shape of a maze, but the dimensions and distances between cells aren't consistent. Currently the software expects consistent spacing between cells and between walls. The maze was only developed to hold a small maze, a total size of 33” x 33” with the panel system. There were some other issues like miscommunications of how wide the cells should be, but we were able to get past these problems by changing how we constructed the maze. To work around this problem the maze was constructed without the use of the tiles and allowed the size of the maze to increase by a factor of 3. Future teams will need to develop a better tiling system if they continue with this type of approach.

## 6. REFERENCES

1. Blom, Jim. “Using Eagle: Schematic.” Using EAGLE: Schematic,
2. learn.sparkfun.com/tutorials/using-eagle-schematic/all.
3. Hmcgrath, and Instructables. “The Basics of SolidWorks: a How-To Guide.” Instructables, Instructables, 20 Oct. 2017, www.instructables.com/The-Basics-of-SolidWorks-A-How-To-Guide/.
4. J. Cai, X. Wan, M. Huo and J. Wu, "An Algorithm of Micromouse Maze Solving," 2010 10th IEEE International Conference on Computer and Information Technology, Bradford, 2010, pp. 1995-2000, doi: 10.1109/CIT.2010.337.
5. https://www.youtube.com/watch?v=1AXwjZoyNno&ab_channel=JeremyBlum
6. Data sheet. . Retrieved from https://www.pololu.com/file/0J86/TB6612FNG.pdf

## APPENDIX I

## Operation Manual

To begin using the micromouse, code will need to be flashed onto the Adafruit Feather from a computer. Our team used the ide CLion to write and compile our software interface that was written in C++. In addition to CLion, MinGW with Platformio will also need to be installed to build and flash our program onto the Feather. Mingw is the software toolchain that will compile the software using GCC.

A comprehensive build guide can be found on our website so that future teams assigned to this project will have a visual guide on project set-up and configuration. This guide will include downloading all the necessary components and each set of software. The image below is a screenshot of CLion and the building platformio building section, used to flash code onto the micromouse. On successful flashing of the Feather, you will receive a success message as seen in the console in the below screenshot.

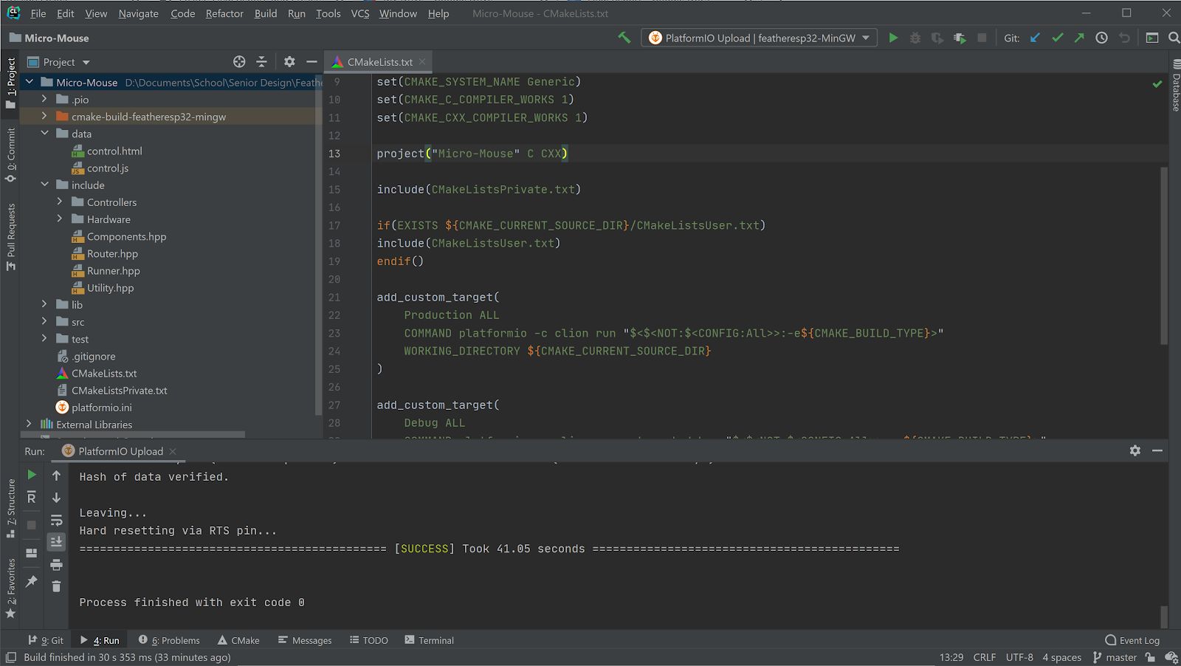
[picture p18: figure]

Figure A.1 CLion

Our current controls for the micromouse are from an Xbox controller with tank drive input. Tank drive means that each analog stick on the controller responds to one wheel of the robot. These settings were used to test new code on the feather along with console outputs on the web ui.

After flashing the feather from CLion the web server should be running so the user needs to connect to the hotspot on the micromouse. This enables the user to run the web UI and successfully connect to micromouse via the websocket. Note that when connected to the micromouse no internet will be available.

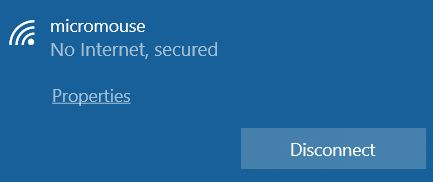
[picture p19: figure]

Figure A.2 Micromouse Connection

Since this device cannot access the internet, multiple workstations are recommended when testing. When our team was testing, we had two members, one connected to the micromouse and the other writing and testing code and flashing it to the micromouse. Since any device can flash the project onto Feather, we found this to be the fastest way to make changes and run these changes. The Adafruit Feather has a light that would turn red to display an input that it was receiving, this was necessary for our group to test because we could use this display to see if the controller was giving the robot commands. This was useful during the testing phase when the controller would lose connection to the computer. We were able to see that the robot was still grabbing commands even after the disconnection, and to solve this problem we added a kill command if the controller input was lost during a run.

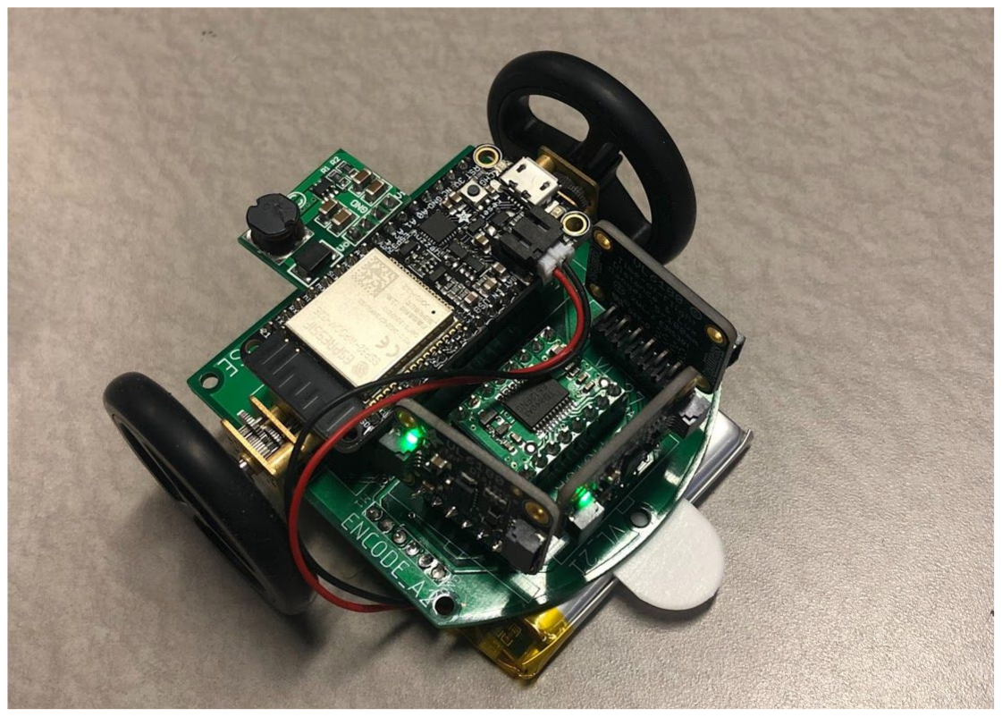
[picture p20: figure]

Figure A.3 Micromouse Prototype

## APPENDIX II

## Alternative/Initial Version

During the design of the micromouse many changes were made with the goal of optimizing the performance of the project while still sticking to the guidelines for a micromouse. Below is a list of initial or altered parts of the micromouse.

- Virtual Micromouse
- PCB
- At the current moment, the PCB has reached Version 4.
■ Version 1 was designed with the idea of being able to place every component on the board while staying within the restriction of a micromouse size. Five holes were made on the board. The largest of the five holes is placed right above the mouse’s encoders. This hole will allow for encoder wires to attach to the encoder above the board and latch on to the PCB underneath. The four other holes are placed to help with keeping the motors in place. In addition, for this version, Eagle’s autorouting feature was used.
■ Version 2 saw the addition of five holes, one at each corner and the fifth at the very front of the board. These holes are added in case mounting components was a desire for the user. For example, the hole at the very front of the board will be used to attach a ski meant to help the mouse run smoother. In addition to this change, the board now has new traces. These traces are easier to follow, but they are still autotraced.
■ Version 3 has manually routed connections. This was done to create more coherent traces that are easier to follow and takes the shortest path between terminals possible. Improvements in performance because of these connections is minimal when compared to previous designs. Feather was turned 180 degrees on board as well to allow for more routing room.
■ Version 4 has new footprints for the updated ToF sensors that are more easily available. This decision also made it so that all needed components may be sourced from one place.

## User Interface

The Graphical User interface (GUI) was the aspect of our project that changed the most. When the project began last semester, Python was chosen to display information to the user along with debugging information that would be useful when our prototype was completed. The first version of the UI (user interface) was simple and had no functionality, however later versions became more robust.

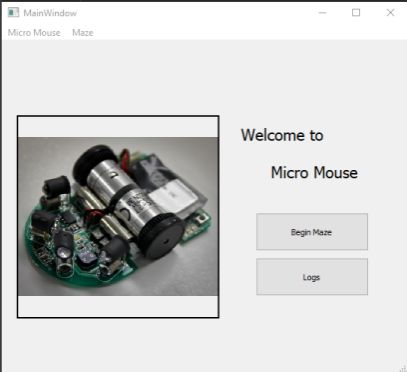
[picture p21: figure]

Figure A.4 UI version 1. Simple layout

This template was shown to the group as a test version of what functionalities were needed and where we could see it being used. This version had a separate window for the actual maze, but nothing was displayed as we didn’t have any of the infrastructure in place to make it usable. When version 2 was being designed we had a better idea of how things were going to be displayed and what was needed. At this point, the web server on the Adafruit Feather was being constructed so a text box was added to allow the user to pass the address of the feather and connect to it. On successful connection a message was displayed to the console as well.

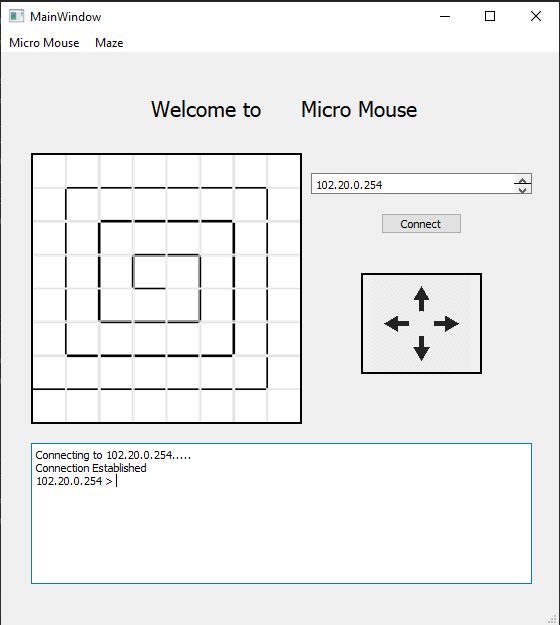
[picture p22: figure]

Figure A.5UI version 2 of the prototype. Web address added

Version 2 of the UI was a big step up as we could now connect to the web server that hosted the Feather. Version 3 was produced as the UI that would be used to test the functionality of the micromouse itself. This version was developed to add functionality of a port to connect to, along with buttons to select between the autonomous and manual mode. These modes would run the robot accordingly when the functionality is added to the micromouse itself. In the end, we did not use this GUI as we implemented a web-based UI.

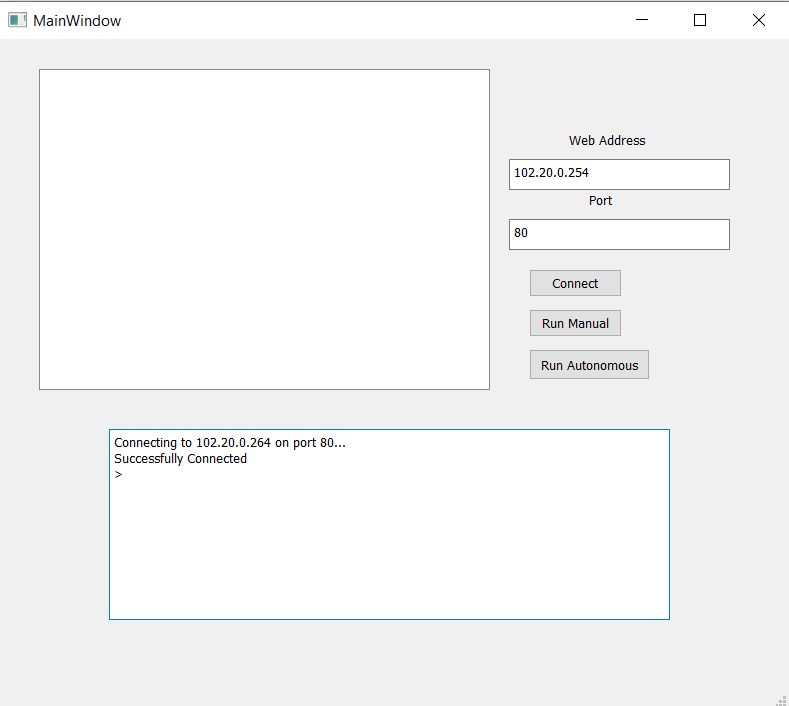
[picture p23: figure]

Figure A.6 Version 3 of the UI. Added connectivity changes and manual/autonomous mode

MAZE

The maze was divided into two parts, the panels and the walls. The walls had to be modified slightly due to miscommunications with the actual size of the micromouse. But in the end, we had a mouse that could navigate the maze within the operational environment that we outlined.

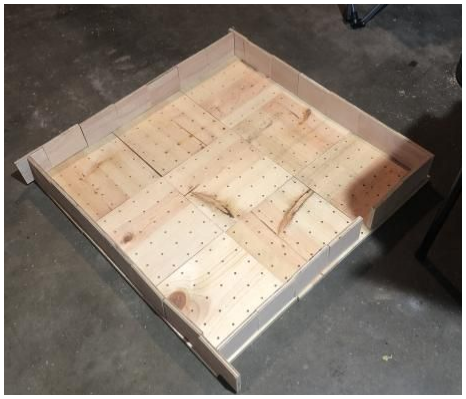
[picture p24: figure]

Figure A.7 Maze Panels

# 1.Appendix III

TYLER

For technical skills I have used python in previous classes for various things, but I had never tried to accomplish this type of functionality in python. Working with the PyQT package I was able to successfully build a GUI that could connect to the micromouse web server, however I was never able to finish the maze mapping to the screen. This was because PyQT did not have a library to draw a dynamic image and update throughout the maze run like I wanted it to. Another reason I was not able to finish this task was because we made the decision to move to a web-based UI so that other members on the team could contribute to the workload. This was not originally in the plan but I was in need of help to finish the UI so making this change seemed like it would have a greater impact on the team instead of myself struggling to figure it out. I was a little disappointed to see the work I had done in the past few months being deprecated, but as we looked into the future this was a necessary move for our team to make to continue work at the pace we needed.

One funny moment I would like to share is when we successfully were able to move the robot with the Xbox controller I finally received the satisfaction of the success our team was having in creating a maze running robot. Seeing the robot move successfully was a step along the way but I feel it was a key moment for our group to boast moral and continue working on our goal.

JORGE

During this project I have refined my ability to self teach in order to learn new material. Picking up a new skill is a difficult task but thankfully when I would get stuck I had the opportunity to bounce ideas around with my team and I found that to be something that I really enjoyed. For example, during this project I learned PCB design and whenever I would hit a wall I could depend on my teammates.

AUSTIN

While working on this project I learned about how project planning is a crucial aspect of any successful project. I learned about the process of implementing hardware together with software in a team environment. Additionally, I learned about the difficulty that adapting to a chaotic world event can place on a project timeline.

While testing on the adafruit feather with the motor controllers and DC to DC boost the wiring became unstable and high voltage was connected to a GPIO pin. this resulted in that feather board being no longer functional. Fortunately the team has just received a new order of components and the team progress was not jeopardized.

RICHARD

While working on this project I got some good experience with c++, which I don't have a ton of experience with, as well as working with a team.

I also gained some good experience with learning how to deal with and work around requirements and limitations. For example, the micromouse only has so much memory that can be used, so the algorithms need to be done in a way that doesn't waste memory, and does not leak any memory.

Another example of a limitation is that the feather uses a specific c++ compiler with a shortened down version of the standard library, so I needed to make sure what I was making was able to compile on the feather as well as still work.

AARON

During this project I learned how to design PCBs from scratch. I normally only write software, so it was interesting to learn how to create hardware. Because I worked on the PCBs, I also learned how to interface the software to the hardware. I ended up learning a lot about IoT devices and how they control hardware over the internet.

It was also interesting to learn how to program a microcontroller. Unlike traditional web applications, microcontrollers have a limited amount of memory and CPU power, making it easy to overwhelm the processor. Designing around this type of hardware was both challenging and fun.

JOSHUA

This project has been a rewarding experience. I gained new skills in PCB designing, and had the opportunity to practice my soldering skills. I am also grateful and honored to be able to work with the members of the team, whom I can confidently say will move on to be bright and competent engineers.

# 2.Appendix IV

The Javascript code that handles movement to the robot via the Xbox controller can be found below. This functionality was much easier to develop due to javascript libraries that were already available to us. A gamepad library was used that allowed us to easily develop and check for inputs on any connected game controller to the computer. This was necessary because the robot needed to be connected to the computer and since the computer could also connect to the controller by bluetooth we could send input from the bluetooth connected controller to our Wi-Fi connected robot. Since all xbox controllers output data the same we were able to test our design with an Xbox elite controller and a Xbox One controller without having to change any code.

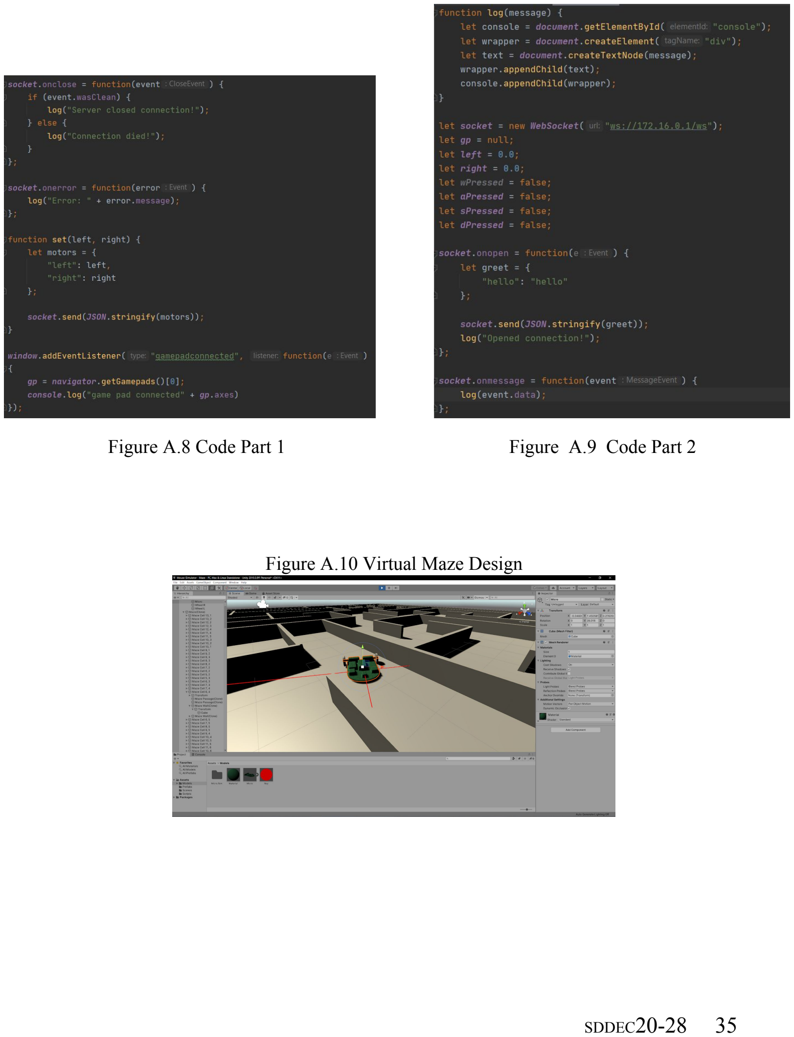
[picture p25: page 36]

Figure A.8 Code Part 1 | Figure A.9 Code Part 2

Figure A.10 Virtual Maze Design

Figure A.11 Virtual Maze Layout


Figure A.12 Virtual Micromouse in Blender


Figure A.13 Importing prototype into Unity


Figure A.14 Standard flood fill algorithm (pseudocode)


Figure A.15 Modified flood fill (partially pseudocode)


Figure A.16 goal searching (partially pseudocode)

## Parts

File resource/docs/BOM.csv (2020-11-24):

Item# | Item type | Qty | Cost | Subtotal | Part# | Supplier | Supplier# | Direct Link
1 | Feather | 1 | $19.95 | $19.95 | 3405 | Digi-Key | 1528-2181-ND | https://www.digikey.com/en/products/detail/adafruit-industries-llc/3405/7244967
2 | Motor Controller | 1 | $3.42 | $3.42 | 713 | Digi-Key | 2183-713-ND | https://www.digikey.com/en/products/detail/pololu-corporation/713/10450399
3 | Magnetic Encoder | 1 | $7.95 | $7.95 | 4761 | Digi-Key | 2183-4761-ND | https://www.digikey.com/en/products/detail/pololu-corporation/4761/11586947
4 | Wheels | 1 | $3.75 | $3.75 | 1452 | Digi-Key | 2183-1452-ND | https://www.digikey.com/en/products/detail/pololu-corporation/1452/10449864
5 | Motors | 2 | $18.95 | $37.90 | 3053 | Digi-Key | 2183-3053-ND | https://www.digikey.com/en/products/detail/pololu-corporation/3053/10450055
6 | DC/DC 3.7 to 12v | 1 | $12.95 | $12.95 | 2895 | Digi-Key | 2183-2895-ND | https://www.digikey.com/en/products/detail/pololu-corporation/2895/10451206
7 | ToF Sensors | 3 | $8.49 | $25.47 | 2489 | Digi-Key | 2183-2489-ND | https://www.digikey.com/en/products/detail/pololu-corporation/2489/10451115
8 | Battery 3.7v (4.2) | 1 | $9.95 | $9.95 | PRT-13813 | Digi-Key | 1568-1492-ND | https://www.digikey.com/en/products/detail/sparkfun-electronics/PRT-13813/6605198
9 | Encoder Wires | 2 | $0.95 | $1.90 | 4762 | Digi-Key | 2183-4762-ND | https://www.digikey.com/en/products/detail/pololu-corporation/4762/11586944
10 | .3.6-pin 0.1" Short Break-away Male Header - Pack of 10 | 1 | $4.95 | $4.95 | 3009 | adafruit |  | https://www.adafruit.com/product/392
11 | 0.1" 36-pin Strip Right-Angle Female/Socket Header (5 pack) | 1 | $2.95 | $2.95 | 1542 | adafruit |  | https://www.adafruit.com/product/598
 | TOTAL | 19 |  | $131.14

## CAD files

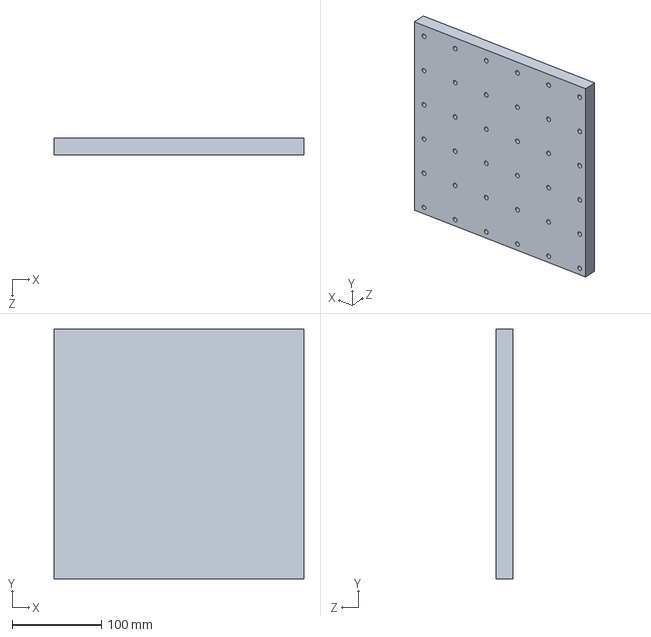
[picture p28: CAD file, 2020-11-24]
resource/maze/Maze_Final.SLDPRT
279.4 x 279.4 x 19.1 mm

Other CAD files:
resource/maze/Maze_Final.DXF

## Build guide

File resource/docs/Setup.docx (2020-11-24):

General Setup for MicroMouse project

First get Mingw from msys2

https://www.msys2.org/

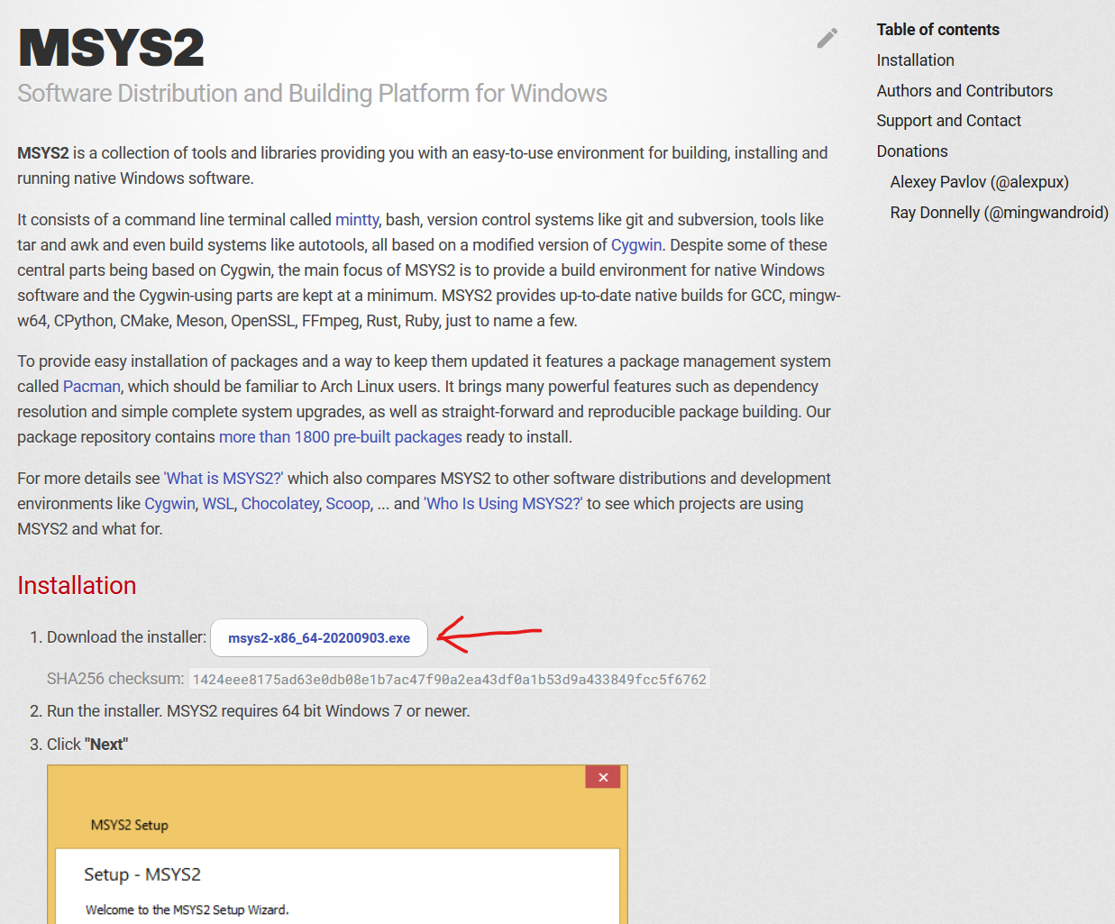
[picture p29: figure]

Save exe, run it

Next, open msys2 terminal and run the following command to get the mingw toolchain (might take a bit)

‘pacman -S mingw-w64-x86_64-toolchain’

Next get jetbrains toolbox, install Clion (you can get them for free from isu here https://it.engineering.iastate.edu/software/students/)

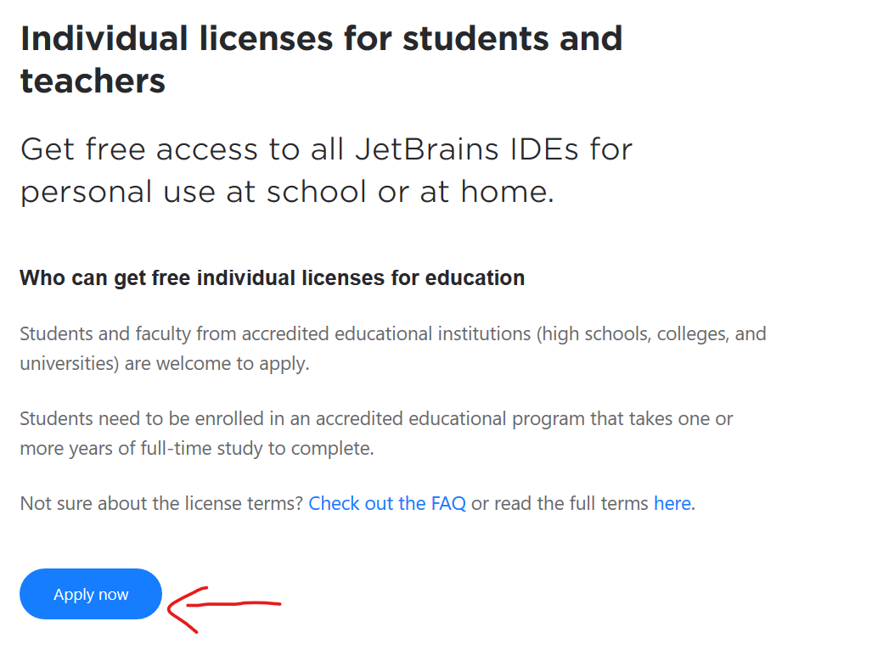
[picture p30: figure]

Apply for license, once you get it download jetbrains toolbox and clion, and provide the license when prompted for it when opening clion for the first time.

Once your in clion, open your settings and navigate to Build, Execution, Deployment -> Toolchains, and make sure you add the mingw toolchain. (you might need to restart clion if it doesn’t show up)

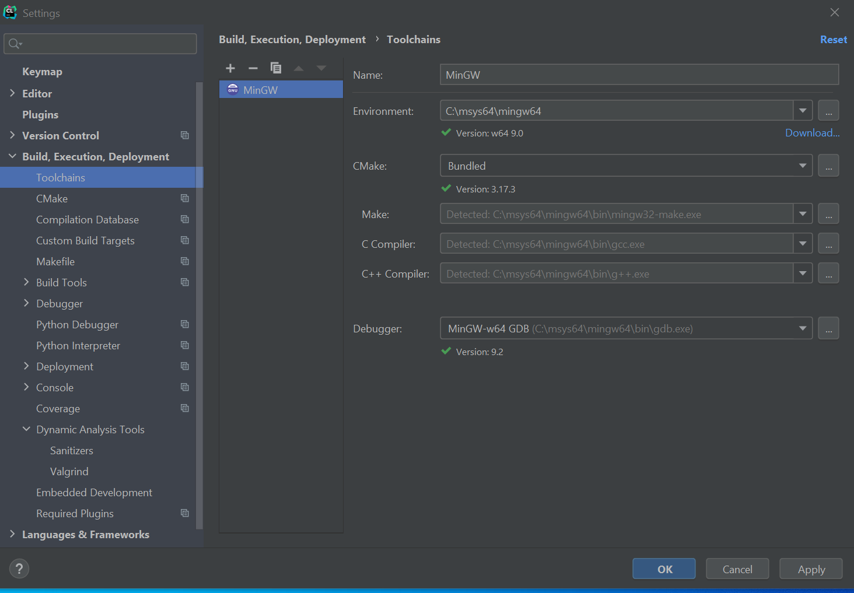
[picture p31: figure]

Once that’s all good, navigate to plugins and install the platformio plugin.

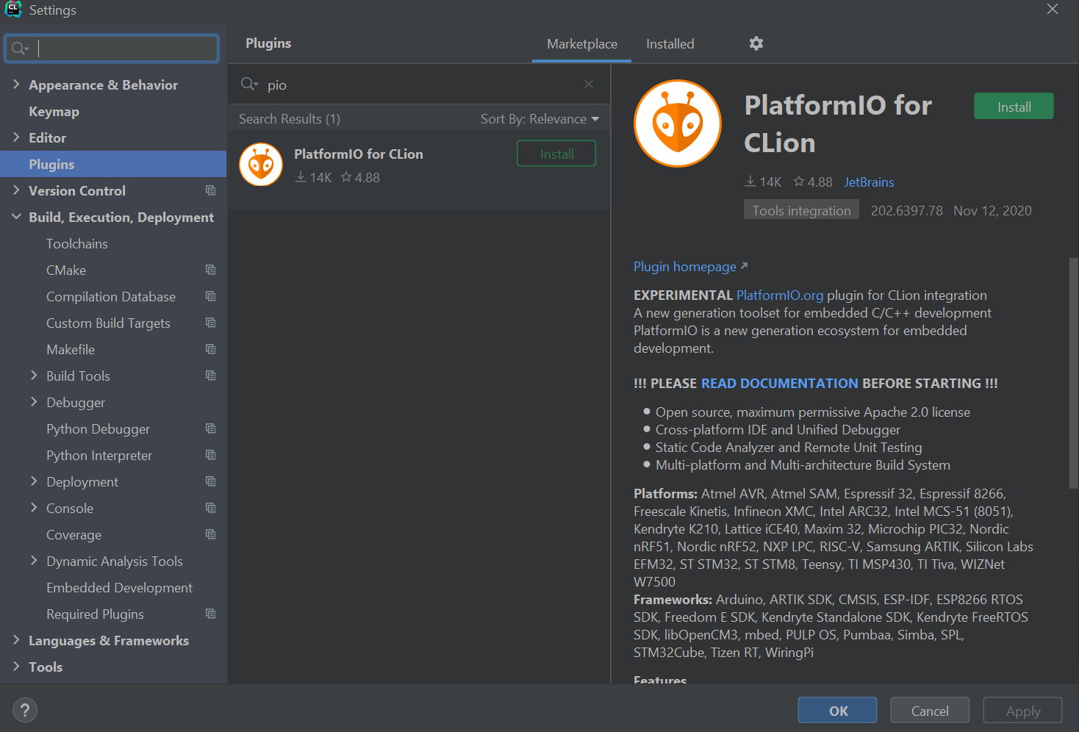
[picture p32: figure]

Next go to the link below and save the page as a python file (.py),

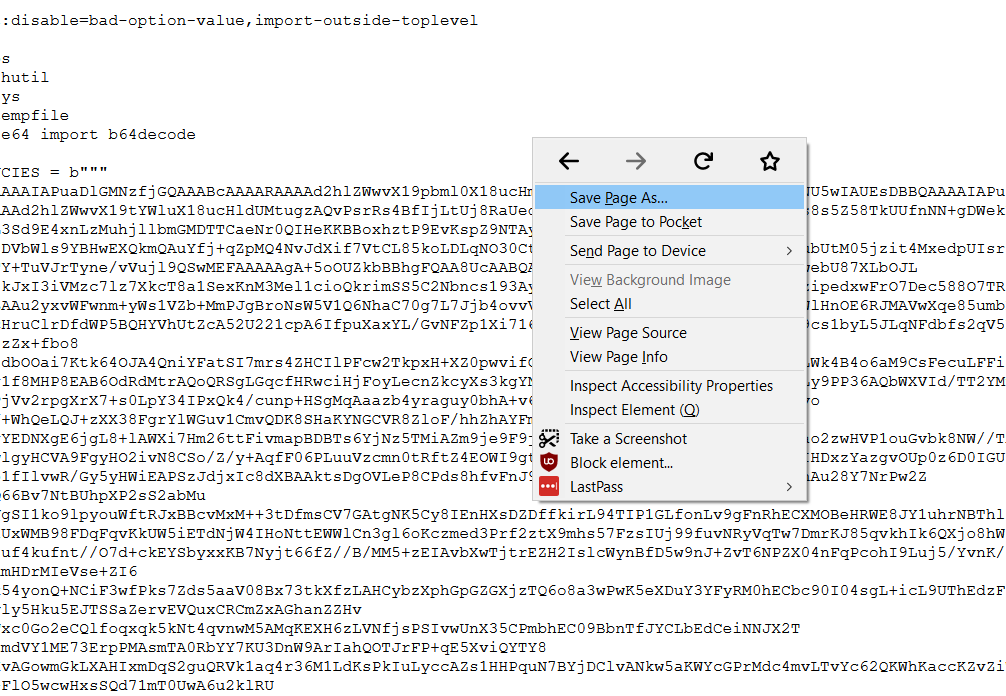
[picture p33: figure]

and then run it using the command below.

‘python get-platformio.py’

After this, you may need to add the path variable.

Add your directory …\.platformio\penv\scripts to the path.

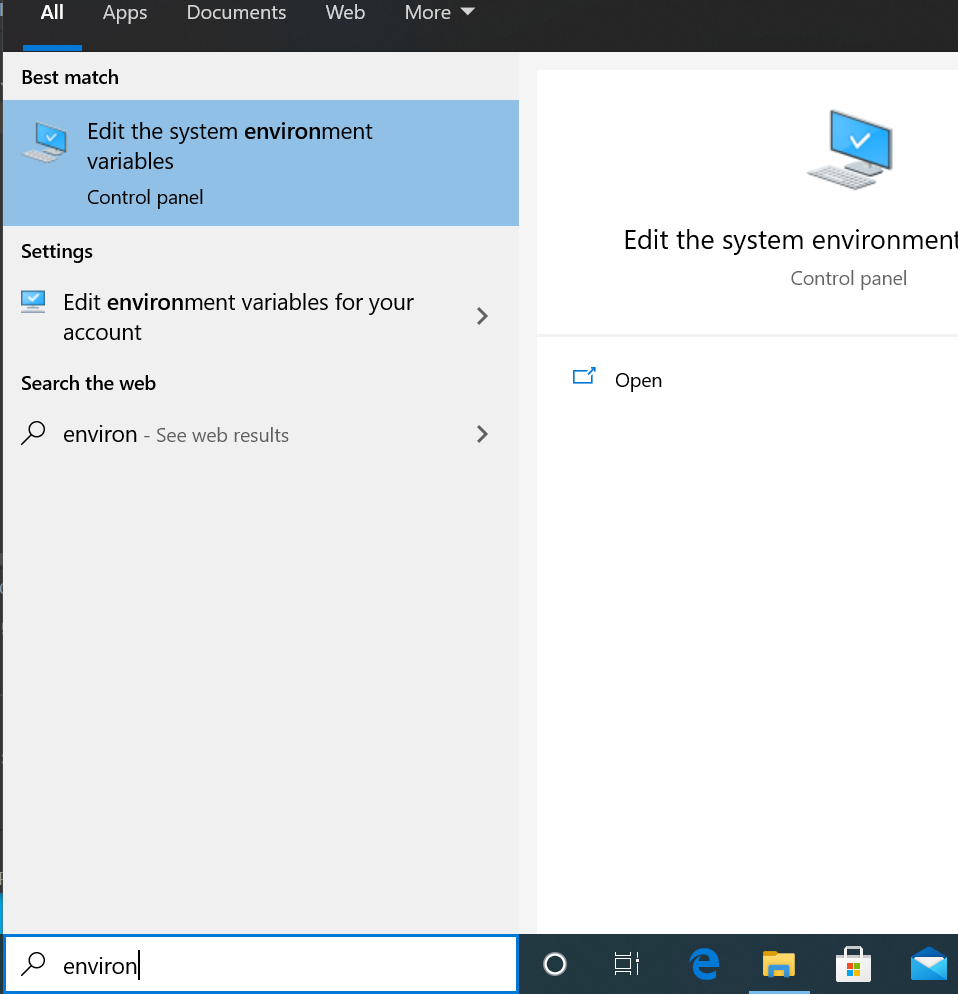
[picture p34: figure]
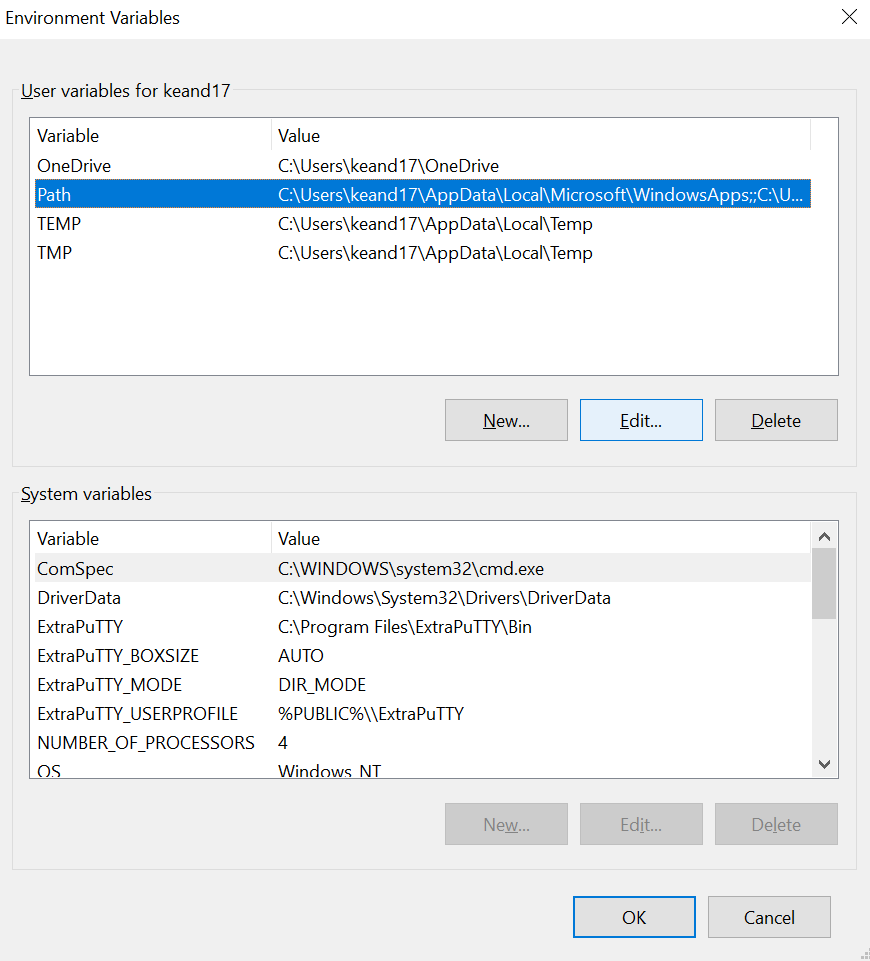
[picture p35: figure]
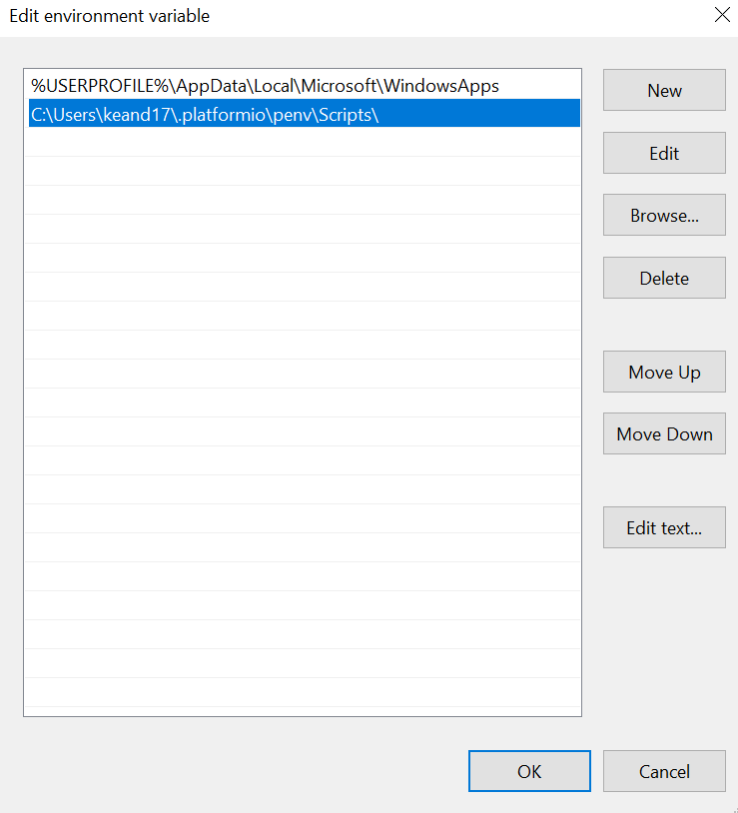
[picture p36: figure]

Once pio is on your path, restart clion, and then open it back up and go to tools -> cmake -> reset cache and reload project.

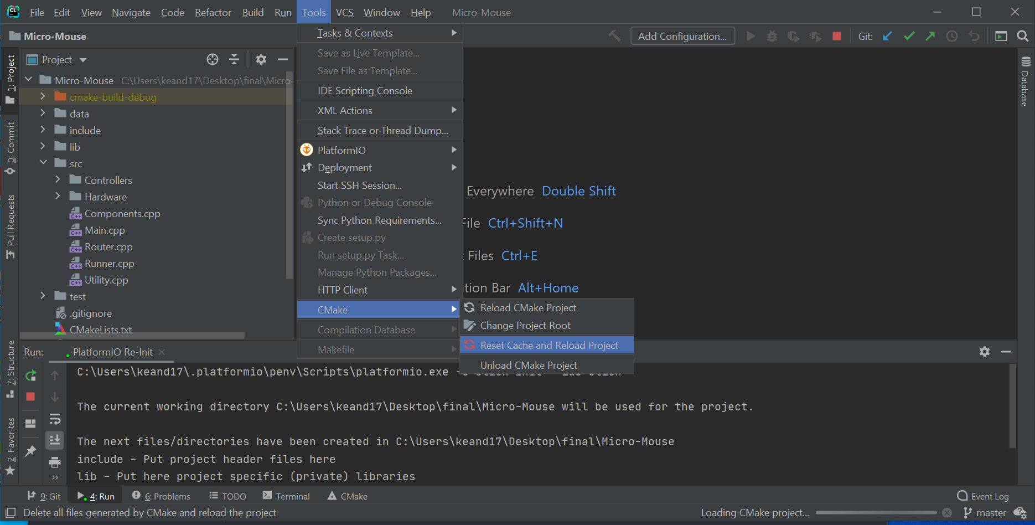
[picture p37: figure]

After this, go back to Build, Execution, Deployment and go to the cmake tab, and make sure the build type is featheresp32.

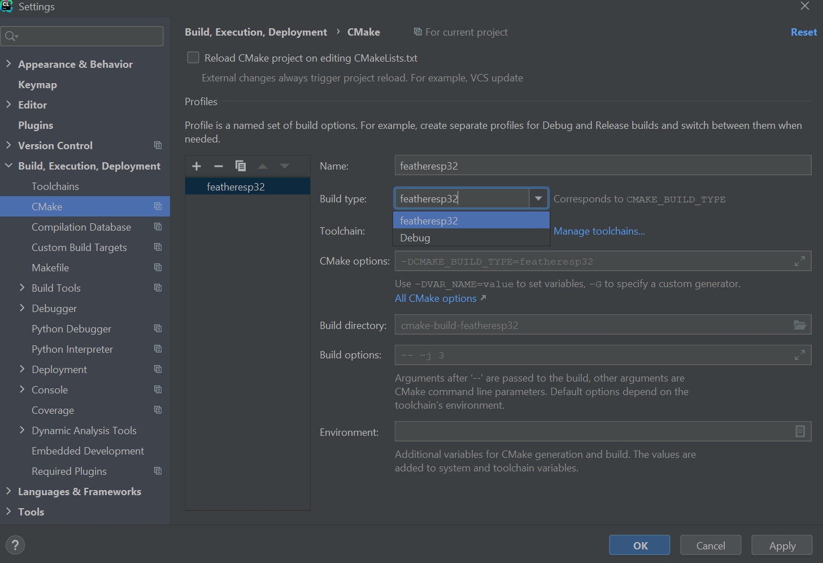
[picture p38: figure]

After all of this, you should be able to exit the menus and build the project.

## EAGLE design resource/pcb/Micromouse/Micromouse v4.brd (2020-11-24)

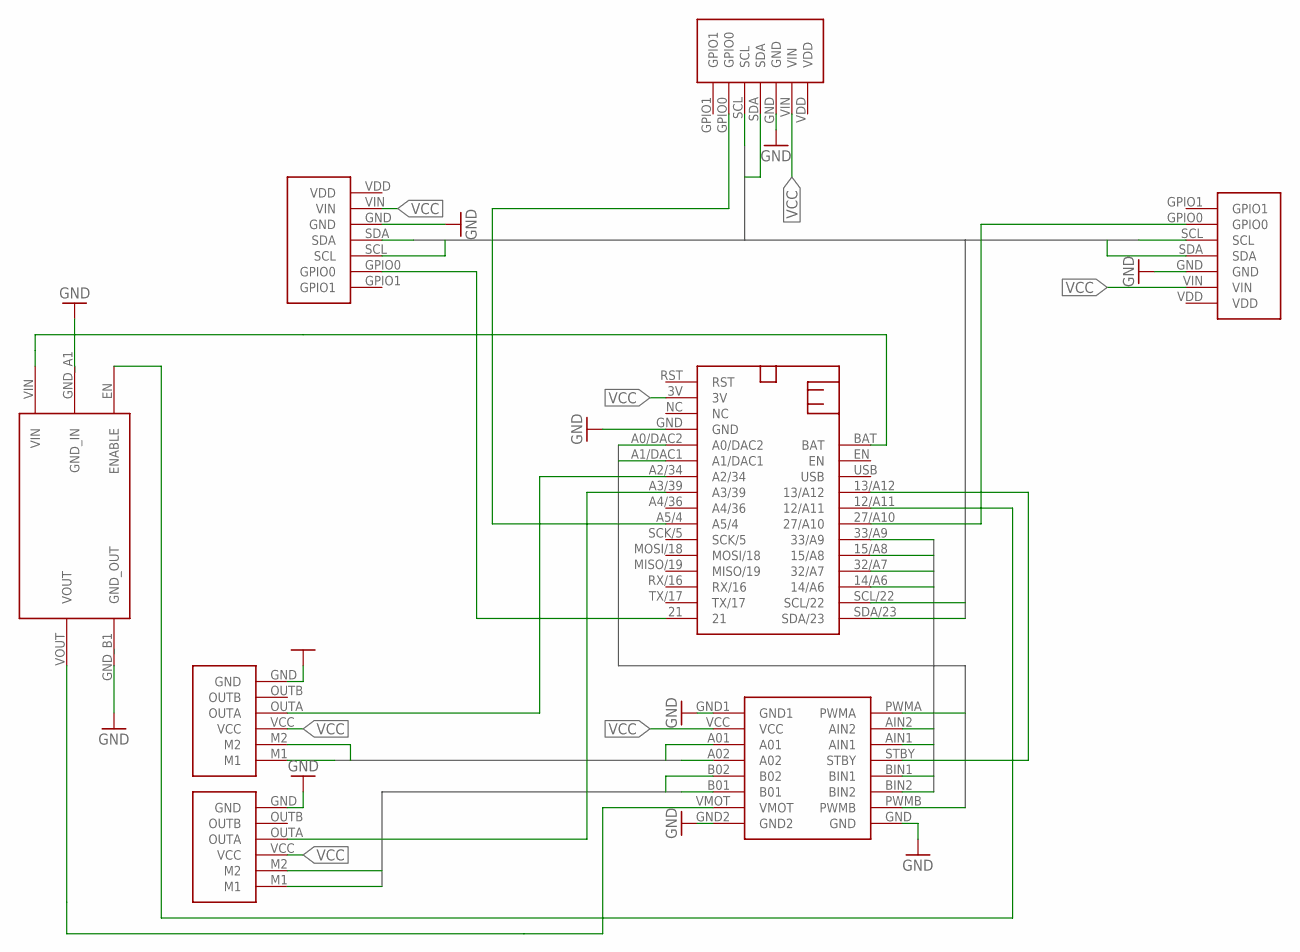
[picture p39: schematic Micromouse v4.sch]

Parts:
12V_BOOST: U3V70F12
ENCODE_A2, ENCODE_A3: ENCODE
ESP1: ESP32
MOTOR1: MOTOR
VL_21, VL_27: VL6180-X
VL_A5: VL6180-X

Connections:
AIN1: ESP1.33/A9, MOTOR1.AIN1
AIN2: ESP1.15/A8, MOTOR1.AIN2
BIN1: ESP1.32/A7, MOTOR1.BIN1
BIN2: ESP1.14/A6, MOTOR1.BIN2
BOOST_IN: 12V_BOOST.VIN, ESP1.BAT
BOOST_OUT: 12V_BOOST.VOUT, MOTOR1.VMOT
GND: 12V_BOOST.GND_A1 (GND_IN), 12V_BOOST.GND_B1 (GND_OUT), ENCODE_A2.GND, ENCODE_A3.GND, ESP1.GND, MOTOR1.GND, MOTOR1.GND1, MOTOR1.GND2, VL_21.GND, VL_27.GND, VL_A5.GND
MA1: ENCODE_A2.M1, MOTOR1.A01
MA2: ENCODE_A2.M2, MOTOR1.A02
MB1: ENCODE_A3.M1, MOTOR1.B01
MB2: ENCODE_A3.M2, MOTOR1.B02
unnamed: 12V_BOOST.EN (ENABLE), ESP1.12/A11
unnamed: ESP1.13/A12, MOTOR1.STBY
unnamed: ENCODE_A2.OUTA, ESP1.A2/34
unnamed: ENCODE_A3.OUTA, ESP1.A3/39
unnamed: ESP1.27/A10, VL_27.GPIO0
unnamed: ESP1.21, VL_21.GPIO0
unnamed: ESP1.A5/4, VL_A5.GPIO0
PWMA: ESP1.A1/DAC1, MOTOR1.PWMA
PWMB: ESP1.A0/DAC2, MOTOR1.PWMB
SCL: ESP1.SCL/22, VL_21.SCL, VL_27.SCL, VL_A5.SCL
SDA: ESP1.SDA/23, VL_21.SDA, VL_27.SDA, VL_A5.SDA
VCC: ENCODE_A2.VCC, ENCODE_A3.VCC, ESP1.3V, MOTOR1.VCC, VL_21.VIN, VL_27.VIN, VL_A5.VIN

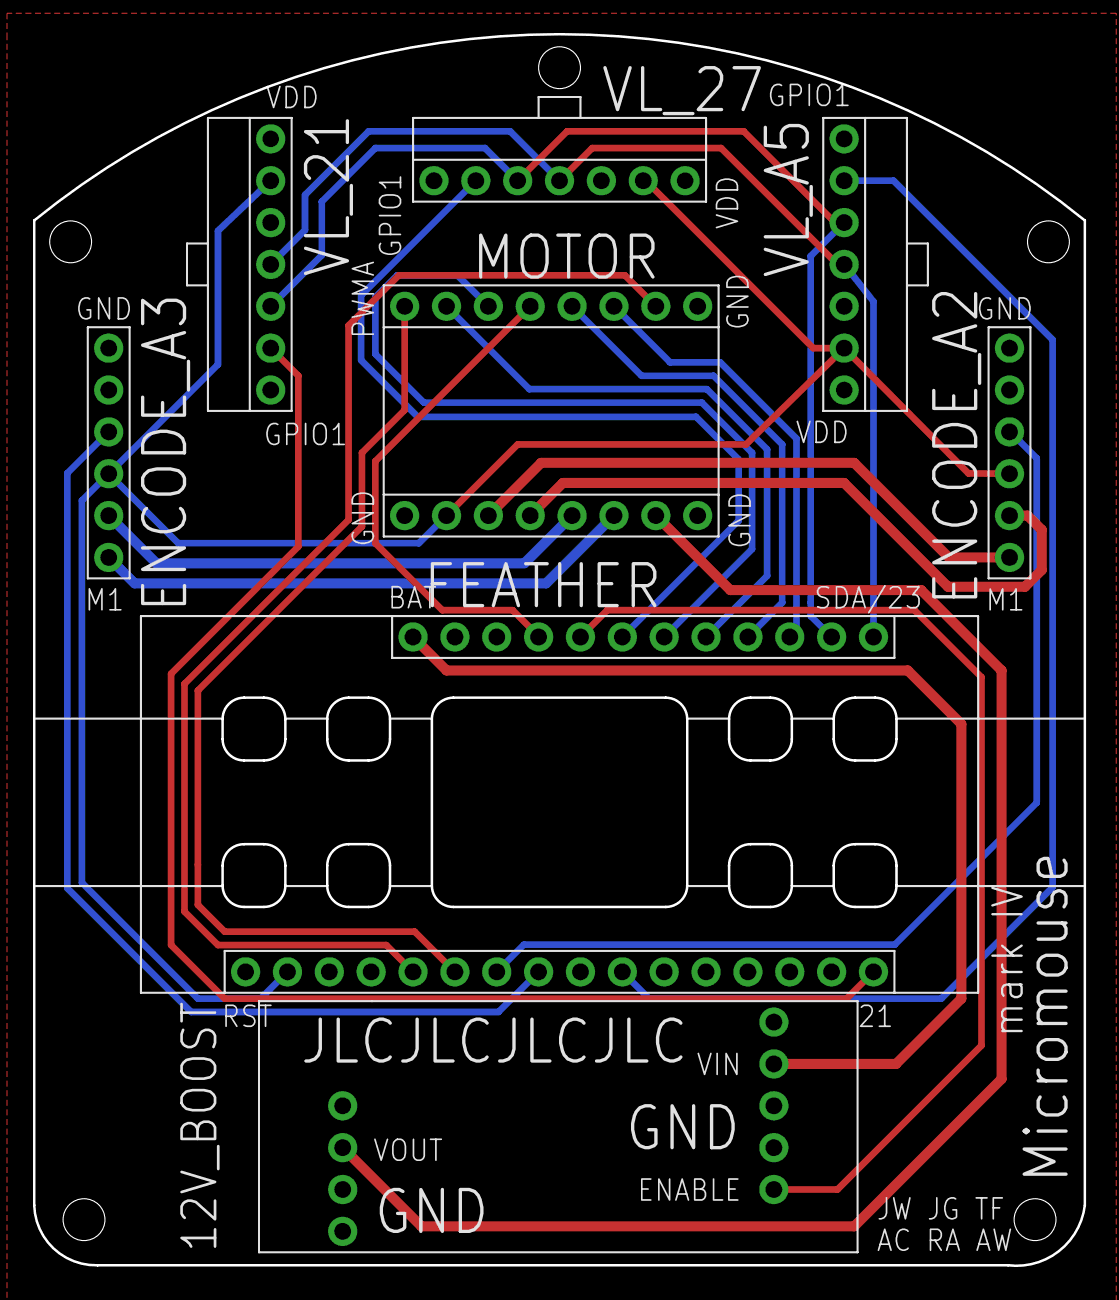
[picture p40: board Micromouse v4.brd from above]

Board: 2 copper layers, 63.8 x 74.7 mm, 8 parts (0 on the bottom side), 23 nets.

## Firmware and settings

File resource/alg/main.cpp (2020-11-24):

#include <iostream>
#include <iomanip>
#include <queue>
#include <string>
#include <math.h>
#include <ctime>
#include <memory>
using namespace std;
using std::hex;
#define WIDTH 15
#define HEIGHT 15
#define NORTH 0
#define EAST 1
#define SOUTH 2
#define WEST 3
#define VISIT 4

#define LEFT 3
#define RIGHT 1

void initGrid();
int toArr( int x, int y );
int legal( int x, int y );
void Visit( int x, int y );
uint8_t grid[WIDTH*HEIGHT];
uint8_t mouseMap[WIDTH*HEIGHT];
//testing still
uint8_t mouseBinMap[WIDTH*HEIGHT];
// 00 0000 - playerOn? visited? northwall? eastwall? southwall? westwall?

int mouseDir=SOUTH; //idk just need something
int xGoal = -1; int yGoal = -1;
int firstIter = 1;

static int closedMap[WIDTH][HEIGHT]; // visited nodes
static int openMap[WIDTH][HEIGHT]; // unvisited nodes
static int dirs[WIDTH][HEIGHT];

static int dx[4]={0, 1, 0, -1};
static int dy[4]={-1, 0, 1, 0};

class node
{
public:

	int xPos;
	int yPos;
	int level;
	int priority;

	node(int xp, int yp, int d, int p)
	{xPos=xp; yPos=yp; level=d; priority=p;}

	void updatePriority(const int & xDest, const int & yDest)
	{
		priority=level+estimate(xDest, yDest)*10; //A*
	}

	// give better priority to going straight instead of diagonally
	void nextLevel(const int & i) // i: direction
	{
		level+=10;
	}

	// Estimation function for the remaining distance to the goal.
	const int & estimate(const int & xDest, const int & yDest) const
	{
		static int xd, yd, d;
		xd=xDest-xPos;
		yd=yDest-yPos;

		d=static_cast<int>(sqrt(xd*xd+yd*yd));
		return(d);
	}
};

// Determine priority (in the priority queue)
bool operator<(const node & a, const node & b)
{
	return a.priority > b.priority;
}

void turn(int leftOrRight) {
	//TODO
	//need to also have mouse physically turn 90 degrees here
	mouseDir = (mouseDir + leftOrRight) % 4;
}

//get dir opposite of direction
int oppositeDir(int direction) {
	return (direction + 2) % 4;
}

//get left dir of direction
int leftDir(int direction) {
	return (direction + 3) % 4;
}

//get right dir of direction
int rightDir(int direction) {
	return (direction + 1) % 4;
}

//turns until mouse is facing direction
void translateToDir(int direction) {
	while(mouseDir != direction) {
		if ((mouseDir + RIGHT) % 4 == direction) turn(RIGHT);
		else turn(LEFT);
	}
}

char mousePiece() {
	return (mouseDir == NORTH) ? '^' :
		   (mouseDir == EAST) ? '>' :
		   (mouseDir == SOUTH) ? 'v' : '<';
}

// A-star
string pathFind(int &xStart, int &yStart, int &xFinish, int &yFinish)
{
	static priority_queue<node> pq[2]; // unvisited nodes
	static int pqi; // pq index
	static int dirIndex, j, x, y, xdx, ydy;
	static char c;
	pqi=0;

	// reset the node maps
	for(y=0;y<WIDTH+1;y++)
	{
		for(x=0;x<HEIGHT+1;x++)
		{
			closedMap[x][y]=0;
			openMap[x][y]=0;
		}
	}

	// create the start node and push into list of open nodes
	shared_ptr<node> n0 = make_shared<node>(xStart, yStart, 0, 0);
	n0->updatePriority(xFinish, yFinish);
	pq[pqi].push(*n0);
	openMap[xStart][yStart]=n0->priority; // mark it on the open nodes map

	// A* search
	while(!pq[pqi].empty())
	{
		// get the current node w/ the highest priority
		// from the list of open nodes
		n0 = make_shared<node>( pq[pqi].top().xPos, pq[pqi].top().yPos, pq[pqi].top().level, pq[pqi].top().priority);

		x=n0->xPos; y=n0->yPos;

		pq[pqi].pop(); // remove the node from the open list
		openMap[x][y]=0;
		// mark it on the closed nodes map
		closedMap[x][y]=1;

		// quit searching when the goal state is reached
		//if((*n0).estimate(xFinish, yFinish) == 0)
		if(x==xFinish && y==yFinish)
		{
			// generate the path from finish to start
			// by following the directions
			string path="";
			while(!(x==xStart && y==yStart))
			{
				j=dirs[x][y];
				c='0'+(j+4/2)%4;
				path=c+path;
				x+=dx[j];
				y+=dy[j];
			}

			// empty the leftover nodes
			while(!pq[pqi].empty()) pq[pqi].pop();
			return path;
		}

		// generate moves (child nodes) in all possible directions
		for(dirIndex=NORTH;dirIndex<=WEST;dirIndex++) {
			xdx=x+dx[dirIndex]; ydy=y+dy[dirIndex];
			if(!(xdx<0 || xdx>WIDTH-1 || ydy<0 || ydy>HEIGHT-1 ||
					(mouseBinMap[toArr(xdx, ydy)] & (1 << oppositeDir(dirIndex))) || closedMap[xdx][ydy]==1))
			{
				shared_ptr<node> m0 = make_shared<node>( xdx, ydy, n0->level, n0->priority);
				m0->nextLevel(dirIndex);
				m0->updatePriority(xFinish, yFinish);

				// add if not in the open
				if(openMap[xdx][ydy]==0)
				{
					openMap[xdx][ydy]=m0->priority;
					pq[pqi].push(*m0);
					dirs[xdx][ydy]=(dirIndex+4/2)%4;
				}
				else if(openMap[xdx][ydy]>m0->priority)
				{
					// update prio
					openMap[xdx][ydy]=m0->priority;
					dirs[xdx][ydy]=(dirIndex+4/2)%4;

					// replace the node with new node
					while(!(pq[pqi].top().xPos==xdx && pq[pqi].top().yPos==ydy))
					{
						pq[1-pqi].push(pq[pqi].top());
						pq[pqi].pop();
					}
					pq[pqi].pop(); // remove the wanted node

					// empty the larger size pq to the smaller one
					if(pq[pqi].size()>pq[1-pqi].size()) pqi=1-pqi;
					while(!pq[pqi].empty())
					{
						pq[1-pqi].push(pq[pqi].top());
						pq[pqi].pop();
					}
					pqi=1-pqi;
					pq[pqi].push(*m0); // add the better node instead
				}
			}
		}
	}
	return "";
}

void initGrid() { for (int i=0; i<(WIDTH+1)*(HEIGHT+1); ++i) grid[i] = 1; }
void initMouseMap() {
	for(int y=0;y<HEIGHT;y++) {
		for (int x = 0; x < WIDTH; x++) {
			if (y==0 || y==HEIGHT-1 || x==0 || x==WIDTH-1) mouseMap[toArr(x, y)] = 1;
			else  mouseMap[toArr(x, y)] = 5;

			if (y==0 || y==HEIGHT-1 || x==0 || x==WIDTH-1) mouseBinMap[toArr(x, y)] = 0b001111;
			else  mouseBinMap[toArr(x, y)] = 0b000000;
		}
	}
}
int toArr(int x, int y) { return y * WIDTH + x; }
int legal(int x, int y) { return !(x < 0 || x >= WIDTH) && !(y < 0 || y >= HEIGHT); }

void mazeGen(int x, int y) {
	grid[toArr(x,y)] = 0;

	int dirs[4] = {NORTH, EAST, SOUTH, WEST};

	for (int i=0; i<4; ++i)
	{
		int r = rand() & 3;
		int temp = dirs[r];
		dirs[r] = dirs[i];
		dirs[i] = temp;
	}
	for (int i=0; i<4; ++i)
	{
		int dx=0, dy=0;
		switch (dirs[i])
		{
			case NORTH: dy = -1; break;
			case SOUTH: dy = 1; break;
			case EAST: dx = 1; break;
			case WEST: dx = -1; break;
		}
		int x2 = x + (dx<<1);
		int y2 = y + (dy<<1);
		if (legal(x2,y2))
		{
			if (grid[toArr(x2,y2)] == 1)
			{
				grid[toArr(x2-dx,y2-dy)] = 0;
				mazeGen(x2,y2);
			}
		}
	}
}

void printMaze(uint8_t maze[], int pX=-1, int pY=-1) {
	for(int y=0;y<HEIGHT;y++)
	{
		for(int x=0;x<WIDTH;x++)
			if(pX==x && pY==y)
				cout<<"\033[1;34m"<<mousePiece()<<"\033[0m";
			else if(maze[toArr(x,y)]==0)
				cout<<".";
			else if(maze[toArr(x,y)]==1)
				cout<<"#"; //obstacle
			else if(maze[toArr(x,y)]==2)
				cout<<"S"; //start
			else if(maze[toArr(x,y)]==3)
				cout<<"*"; //route
			else if(maze[toArr(x,y)]==4)
				cout<<"F"; //finish
			else if(maze[toArr(x, y)]==5)
				cout<<"?"; //unknown
			else if(maze[toArr(x, y)]==6)
				cout<<"\033[1;31mv\033[0m"; //visited
		cout<<endl;
	}
	cout<<endl;
}

void cleanMaze(uint8_t maze[]) {
	for(int y=0;y<HEIGHT;y++) {
		for(int x=0;x<WIDTH;x++) {
			if(maze[toArr(x, y)]==5 || maze[toArr(x, y)]==6 || maze[toArr(x, y)] == 7) maze[toArr(x,y)]=0;
		}
	}
}

void printBinMap() {
	for(int y=0;y<HEIGHT;y++) {
		for(int x=0;x<WIDTH;x++) {
			printf("%01x", mouseBinMap[toArr(x, y)]);
		}
		cout<<endl;
	}
	cout<<endl;
}

//trust me :)
void setWalls(int x, int y, int l, int f, int r) {
	//set current walls
	mouseBinMap[toArr(x, y)] = (((mouseBinMap[toArr(x, y)] |= (l << leftDir(mouseDir))) |= (f << mouseDir)) |= (r << rightDir(mouseDir)));
	//also set same wall for neighbors
	mouseBinMap[toArr(x+dx[leftDir(mouseDir)], y+dy[leftDir(mouseDir)])] |= (l << rightDir(mouseDir));
	mouseBinMap[toArr(x+dx[mouseDir], y+dy[mouseDir])] |= (f << oppositeDir(mouseDir));
	mouseBinMap[toArr(x+dx[rightDir(mouseDir)], y+dy[rightDir(mouseDir)])] |= (r << leftDir(mouseDir));
}

void scanBitNear(int currX, int currY) {
	//TODO
	//instead of updating using grid, we would just update mouse map with each scanners results
	// would instead use scanner input, assign 0 if nothing in next cell (dist > a number) else 1 (dist < a number)

	//left scanner, middle scanner, right scanner
	mouseMap[toArr(currX+dx[leftDir(mouseDir)], currY+dy[leftDir(mouseDir)])] = grid[toArr(currX+dx[leftDir(mouseDir)], currY+dy[leftDir(mouseDir)])];
	mouseMap[toArr(currX+dx[mouseDir], currY+dy[mouseDir])] = grid[toArr(currX+dx[mouseDir], currY+dy[mouseDir])];
	mouseMap[toArr(currX+dx[rightDir(mouseDir)], currY+dy[rightDir(mouseDir)])] = grid[toArr(currX+dx[rightDir(mouseDir)], currY+dy[rightDir(mouseDir)])];

	setWalls(currX, currY,
			(grid[toArr(currX+dx[leftDir(mouseDir)], currY+dy[leftDir(mouseDir)])] == 1),
			(grid[toArr(currX+dx[mouseDir], currY+dy[mouseDir])] == 1),
			(grid[toArr(currX+dx[rightDir(mouseDir)], currY+dy[rightDir(mouseDir)])] == 1)
	);
}

//maybe this will be used one day lol
void calculateGoal() {
	for(int y=0;y<HEIGHT-1;y++) {
		for(int x=0;x<WIDTH-1;x++) {
			//check if there exists a goal loop in the maze
			if (((!(mouseBinMap[toArr(x, y)] & (1 << SOUTH))) && (!(mouseBinMap[toArr(x, y)] & (1 << EAST)))) &&
				((!(mouseBinMap[toArr(x+1, y)] & (1 << WEST))) && (!(mouseBinMap[toArr(x+1, y)] & (1 << SOUTH)))) &&
				((!(mouseBinMap[toArr(x, y+1)] & (1 << EAST))) && (!(mouseBinMap[toArr(x, y+1)] & (1 << NORTH)))) &&
				((!(mouseBinMap[toArr(x+1, y+1)] & (1 << WEST))) && (!(mouseBinMap[toArr(x+1, y+1)] & (1 << NORTH)))))
			{
				xGoal = x;
				yGoal = y;
				cout<<"found goal at ("<<xGoal<<", "<<yGoal<<")"<<endl;
				return;
			}

		}
	}
	cout<<"404 goal not found"<<endl;
}

void moveForward(int x, int y) {
	//TODO

	printMaze(mouseMap, x, y);
//	printBinMap();
	getchar();

	return; //need to physically move mouse 1 cell
}

void flood(int startX, int startY) {
	int currDir = mouseDir;

	//update mouse map with scanners
	scanBitNear(startX, startY);

	// Go forward if cell in front is accessible
	if ((!(mouseBinMap[toArr(startX, startY)] & (1 << currDir))) && (!(mouseBinMap[toArr(startX+dx[currDir], startY+dy[currDir])] & (1 << VISIT)))) {
		//visited
		mouseBinMap[toArr(startX, startY)] |= (1 << VISIT);
		//unimplemented, physically move mouse forward
		moveForward(startX+dx[currDir], startY+dy[currDir]);
		//recurse to the cell ahead
		flood(startX+dx[currDir], startY+dy[currDir]);
	}

	// Go left
	if ((!(mouseBinMap[toArr(startX, startY)] & (1 << leftDir(currDir)))) && (!(mouseBinMap[toArr(startX+dx[leftDir(currDir)], startY+dy[leftDir(currDir)])] & (1 << VISIT)))) {

		//make sure were actually going left, mousedir might have changed
		translateToDir(leftDir(currDir));
		mouseBinMap[toArr(startX, startY)] |= (1 << VISIT);
		moveForward(startX+dx[leftDir(currDir)], startY+dy[leftDir(currDir)]);
		flood(startX+dx[leftDir(currDir)], startY+dy[leftDir(currDir)]);
	}

	// Go right
	if ((!(mouseBinMap[toArr(startX, startY)] & (1 << rightDir(currDir)))) && (!(mouseBinMap[toArr(startX+dx[rightDir(currDir)], startY+dy[rightDir(currDir)])] & (1 << VISIT)))) {
		translateToDir(rightDir(currDir));
		mouseBinMap[toArr(startX, startY)] |= (1 << VISIT);
		moveForward(startX+dx[rightDir(currDir)], startY+dy[rightDir(currDir)]);
		flood(startX+dx[rightDir(currDir)], startY+dy[rightDir(currDir)]);
	}

	translateToDir(oppositeDir(currDir));
	moveForward(startX, startY);
	mouseBinMap[toArr(startX, startY)] |= (1 << VISIT);

	return;
}

vector<int> toInstructs(string& route)
{
	int counter=0;
	char last='x';
	vector<int> instructs;

	int len = route.length() -1;
	for(int i=0; i<= len; i++) {
		if (route[i] == last || last == 'x') {counter++;}
		else if (i != len) {
			instructs.push_back(counter);
			counter=1;
			if ((last=='0' && route[i] == '1') ||
				(last=='1' && route[i] == '2') ||
				(last=='2' && route[i] == '3') ||
				(last=='3' && route[i] == '0')) instructs.push_back(0);
			else if ((last=='0' && route[i] == '3') ||
					(last=='1' && route[i] == '0') ||
					(last=='2' && route[i] == '1') ||
					(last=='3' && route[i] == '2')) instructs.push_back(-1);
		}
		last = route[i];
		if (i == len) instructs.push_back(counter);
	}
	return instructs;
}

int main() {
	srand(time(NULL));

	// create empty map
	initGrid();
	printMaze(grid);

	//create empty mouse map
	initMouseMap();

	// make maze
	mazeGen(1,1);

	// fresh map
	printMaze(grid);

	int xS=1, yS=1;
	int startDir = mouseDir;

	printMaze(mouseMap);

	//flood then clean
	flood(xS, yS);
	translateToDir(startDir);
	cleanMaze(mouseMap);

	//print mouse and mousebin maps, then calculate goal
	printMaze(mouseMap);
	printBinMap();
	calculateGoal();

	if (xGoal == -1 && yGoal == -1){
		xGoal=HEIGHT-2;
		yGoal=WIDTH-2;
	}

	cout<<"starts at ("<<xS<<","<<yS<<')'<<endl;
	cout<<"ends at ("<<xGoal<<","<<yGoal<<')'<<endl;

	//a*
	string route=pathFind(xS, yS, xGoal, yGoal);
	vector<int> instructs = toInstructs(route);

	if(route.length()>0)
	{
		int j;
		int x=xS;
		int y=yS;
		mouseMap[ toArr(x,y) ]=2;

		for(int i=0;i<route.length();i++)
		{
			j = route[i] - 48;
			x=x+dx[j];
			y=y+dy[j];
			mouseMap[toArr(x,y)]=3;
		}

		mouseMap[toArr(x,y)]=4;

		//instructions
		for(int i=0; i<=instructs.size()-1; i++){
			switch (instructs[i]) {
				case -1: cout<<"left turn"<<endl;break;
				case 0: cout<<"right turn"<<endl;break;
				default : cout<<"forward "<<instructs[i]<<endl;break;
			}
		}

		// display the map with the route
		printMaze(mouseMap);
	}
	return(-1);
}

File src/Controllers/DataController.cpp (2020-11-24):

#include "Controllers/DataController.hpp"

#include "Components.hpp"
#include "Hardware/RangeComponent.hpp"
#include "Hardware/MotorComponent.hpp"
#include "Hardware/EncoderComponent.hpp"
#include "Runner.hpp"

#include <ESPAsyncWebServer.h>

using Request = AsyncWebServerRequest;

namespace Maze {
	DataController::~DataController() = default;

	void DataController::status(Request* r) {
		ArduinoJson::DynamicJsonDocument doc(1024);
		std::array<RangeComponent*, 3> sensors = {
				&_components.rangeFront(),
				&_components.rangeLeft(),
				&_components.rangeRight()
		};

		std::array<MotorComponent*, 2> motors = {
				&_components.motorLeft(),
				&_components.motorRight()
		};

		std::array<EncoderComponent*, 2> encoders = {
				&_components.encoderLeft(),
				&_components.encoderRight()
		};

		auto dataSensors = doc.createNestedObject("sensors");
		for (const auto* sensor : sensors) {
			auto json = dataSensors.createNestedObject(sensor->name());
			json["range"] = sensor->getRange();
			json["message"] = sensor->getMessage();
			json["ms"] = sensor->getTime();
			json["ms"] = sensor->getTime();
		}

		auto dataMotors = doc.createNestedObject("motors");
		for (const auto* motor : motors) {
			auto json = dataMotors.createNestedObject(motor->name());
			json["speedTarget"] = motor->getSpeedTarget();
			json["speedCurrent"] = motor->getSpeedCurrent();
		}

		auto dataEncoders = doc.createNestedObject("encoders");
		for (const auto* encoder : encoders) {
			auto json = dataEncoders.createNestedObject(encoder->name());
			json["ticks"] = encoder->getTicks();
			json["distance"] = encoder->getDistance();
		}

		doc["msProcess"] = _components.runner().getTimeCompute();
		doc["msLoop"] = _components.runner().getTimeLoop();

		send(200, r, doc, __func__);
	}
}

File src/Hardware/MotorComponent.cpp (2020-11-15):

#include "Hardware/MotorComponent.hpp"

#include "Utility.hpp"

#include <Arduino.h>

#define LEDC_BASE_FREQ     5000
#define LEDC_TIMER_13_BIT  13
#define LEDC_TIMER_13_BIT_MAX 8191

namespace Maze {
	MotorComponent::MotorComponent(uint8_t pin1, uint8_t pin2, uint8_t pinPWM, uint8_t channel, bool reverse, const char* name) :
			_pin1(pin1),
			_pin2(pin2),
			_channel(channel),
			_reverse(reverse),
			_enabled(false),
			_name(name) {
		pinMode(pin1, OUTPUT);
		pinMode(pin2, OUTPUT);
		ledcSetup(channel, LEDC_BASE_FREQ, LEDC_TIMER_13_BIT);
		ledcAttachPin(pinPWM, channel);
	}

	void MotorComponent::setSpeed(double speed) {
		auto limit = clamp(speed, -1.0, 1.0);
		if (_reverse) limit *= -1.0;
		_speedTarget = limit;
	}

	void MotorComponent::loop(double dilation) {
		const double ACCELERATION = 0.5;

		double sign = _speedTarget < 0 ? -1.0 : 1.0;
		if (abs(_speedCurrent) < abs(_speedTarget)) {
			_speedCurrent += ACCELERATION * dilation * sign;
		} else {
			_speedCurrent = _speedTarget;
		}

		if (_speedCurrent > 0.01) {
			// Clockwise
			digitalWrite(_pin1, HIGH);
			digitalWrite(_pin2, LOW);
			double multiplier = LEDC_TIMER_13_BIT_MAX;
			uint32_t duty = multiplier * _speedCurrent;
			ledcWrite(_channel, duty);
			_enabled = true;
		} else if (_speedCurrent < -0.01) {
			// Counterclockwise
			digitalWrite(_pin1, LOW);
			digitalWrite(_pin2, HIGH);
			double multiplier = LEDC_TIMER_13_BIT_MAX;
			uint32_t duty = -1.0 * multiplier * _speedCurrent;
			ledcWrite(_channel, duty);
			_enabled = true;
		} else {
			// Stop
			digitalWrite(_pin1, LOW);
			digitalWrite(_pin2, LOW);
			ledcWrite(_channel, 0);
			_enabled = false;
		}
	}
}

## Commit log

2020-10-08 Make web framework
2020-10-10 Added the sensor
2020-10-14 Add printf.
2020-10-14 Sensor timeout
2020-11-05 Sensor init and motor driver
2020-11-06 Make motors work
2020-11-07 Joystick support for wheel speed
2020-11-15 Add encoders to code.
2020-11-24 Add PCB resources.
    [Micromouse v2.brd, Micromouse v2.sch, Micromouse v4.brd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]
2020-11-24 Updated PCB
    [Micromouse v4.brd, Micromouse v4.sch]
2020-11-24 Added Maze files
    [Maze_Final.DXF, Maze_Final.SLDPRT]
2020-11-24 Add Bill of Materials
    [BOM.csv]
